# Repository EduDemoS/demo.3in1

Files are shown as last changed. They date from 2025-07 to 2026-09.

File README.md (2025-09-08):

# 3×1 Demonstrator: Solar, wind and water harvesting in a single educational project

The 'Edudemos' project launches an innovative 3×1 demonstrator that combines three powerful educational resources in a single device. This multifunctional demonstrator allows students to explore and experiment with solar energy harvesting, wind energy, and water harvesting, all in a single project.

The 3×1 demonstrator is designed for students in vocational training centers and schools to build with the help of their teachers, integrating fundamental concepts of renewable energy and resource management.

This repository contains all necessary files and is structured as follows:

- [doc](doc) contains documentation such as 
  - [details.md](doc/details.md)
  - assembly manual
  - bill of material
- [code](code) contains program code to run the model
- [model](model) contains the printable 3D model

# Licensing
Please note: different licenses apply depending on the type of content.

All documents and 3d models (files ending with .pdf and .stl) are licensed under [CC-BY-NC-SA 4.0](https://creativecommons.org/licenses/by-nc-sa/4.0/).

All files containing code are licensed under [GNU GPL V3](https://www.gnu.org/licenses/gpl-3.0.txt).

# Disclaimer
Funded by the European Union. Views and opinions expressed are however those of the author(s) only and do not necessarily reflect those of the European Union or the European Education and Culture Executive Agency (EACEA). Neither the European Union nor EACEA can be held responsible for them.

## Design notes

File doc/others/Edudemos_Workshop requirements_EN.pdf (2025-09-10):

# EDUcating through Sustainable DEMOnstrators

# Workshop requirements

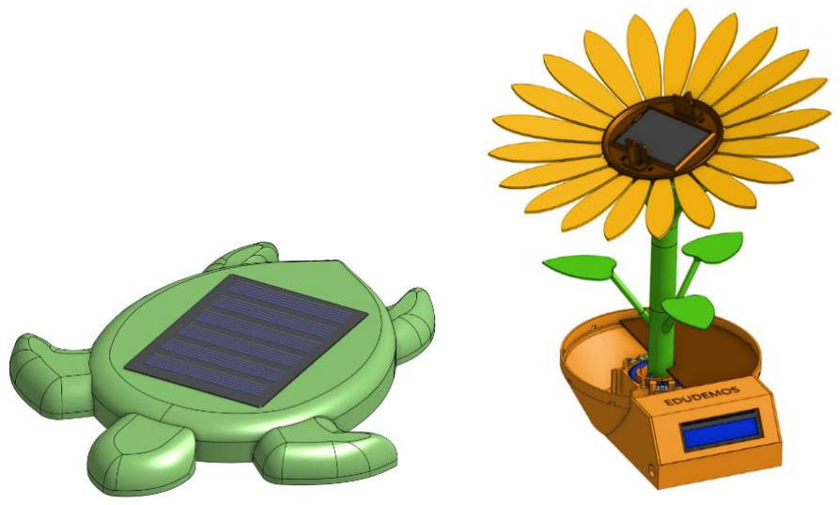
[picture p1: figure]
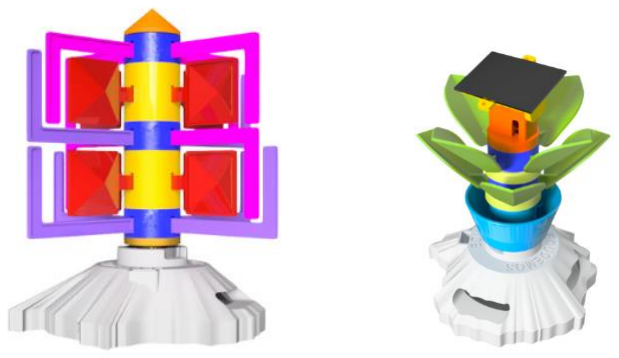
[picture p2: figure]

Funded by the European Union. Views and opinions expressed are however those of the author(s) only and do not necessarily reflect those of the European Union or the European Education and Culture Executive Agency (EACEA). Neither the European Union nor EACEA can be held responsible for them.

EduDemoS 3in1 © 2025 by Gerda Stetter Stiftung – Technik macht Spaß! is licensed under Creative Commons Attribution-NonCommercial-ShareAlike 4.0 International. To view a copy of this license, visit https://creativecommons.org/licenses/by-nc-sa/4.0/

# EduDemoS Workshop

During the EduDemoS Workshop we will develop three different Sustainable Demonstrators:

### 1. Turtle

2. 3x1 Modular Demonstrator

### 3. Sun-Tracker (Sunflower)

To know more about these demonstrators and the EduDemoS Project, visit the website https://edudemos.eu/en/

Every demonstrator has a guide explaining how to build it. To be prepared for the Workshop, you can download and read these guides beforehand.

- From the homepage of the website, click on Demonstrators in the top menu. Look for Turtle, Solar-Tracking and 3x1 Demonstrator, then select Guide for each of them and download the pdf file.
- For the 3x1 Demonstrator you can download the guide in English or Spanish. See the name of the file to identify them.
- There are also some videos that illustrate how to assemble the 3x1 demonstrator.

# Technical requirements

To be able to successfully complete the Edudemos Workshop, you will need the following:

- Bring your laptop
- Have Arduino IDE installed
- Have the boards ESP8266 and ESP32 installed in Arduino
- Have the necessary libraries installed in Arduino
- Have the CP210x Driver installed

Below there is a guide explaining how to download and install everything you need.

# Installation Guide

# What is the Arduino IDE?

The Arduino IDE (Integrated Development Enviroment) is the software used to write, compile and upload code to your board. (In this case the ESP32-WROOM-DA and the ESP8266.)

# Downloading and installing the Arduino IDE:

### Step 1: Go to the Arduino Website

Open your web browser and visit the official Arduino website: https://www.arduino.cc/

### Step 2: Navigate to the Arduino IDE Download Page

From the homepage, click on Products in the top menu. Look for Software, then select Arduino IDE. Or go directly to this link: https://www.arduino.cc/en/software/#ide

### Step 3: Choose Your Operating System

On the Downloads page, select the appropriate version of the Arduino IDE for your operating system (Windows, macOS, or Linux).

- Recommended donwload: Windows Win 10 and newer, 64 bits

### Step 4: Download the Installer

Click on the download link, and if prompted, you can choose to contribute or simply click just download without contributing.

### Step 5: Install the Arduino IDE

- For Windows:
- Run the downloaded .exe file.
- Follow the installation wizard to install the IDE.
- Check the option to install the USB driver when prompted.
- For macOS:
- Open the downloaded .dmg file.
- Drag the Arduino IDE to the Applications folder.
- For Linux:
- Extract the downloaded .tar.xz file.
- Run the install.sh script in the terminal.

### Step 6: Verify Installation

Open the Arduino IDE to ensure it launches correctly.

# Cofiguring the Arduino IDE for the Sunflower and Turtle Demonstrators:

### Step 1: Add the ESP8266 Board URL

To use the ESP8266 with the Arduino IDE, you need to include the appropriate URL in the IDE's preferences:

1. Open the Arduino IDE
2. Go to File > Preferences (on macOS, this might be under Arduino > Preferences)
3. In the Additional Board Manager URLs field, paste the following URL: http://arduino.esp8266.com/stable/package_esp8266com_index.json
4. If there are already other URLs listed, separate them with a comma
5. Activate Auto save and Automatic and then click OK. See the image below

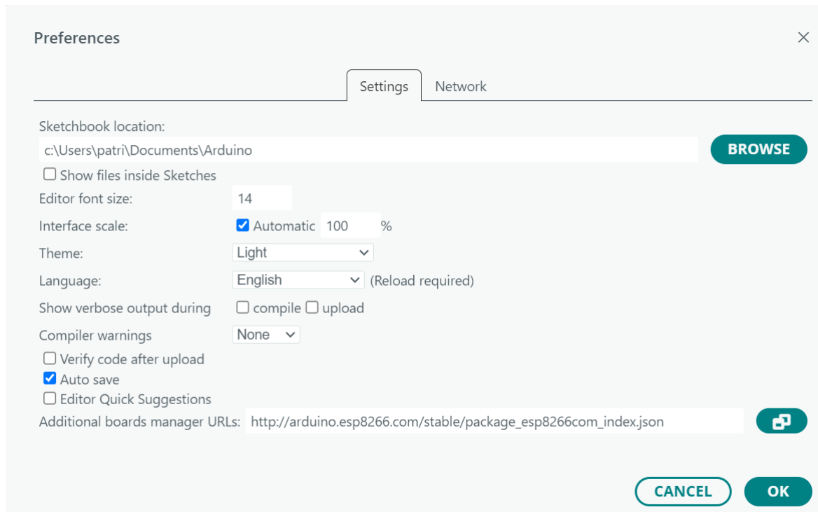
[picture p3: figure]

### Step 2: Install the ESP8266 Board Package

1. Go to Tools > Board > Boards Manager
2. In the search bar, type ESP8266
3. Select esp8266 by ESP8266 Community and click Install/update
4. Wait for the installation to complete

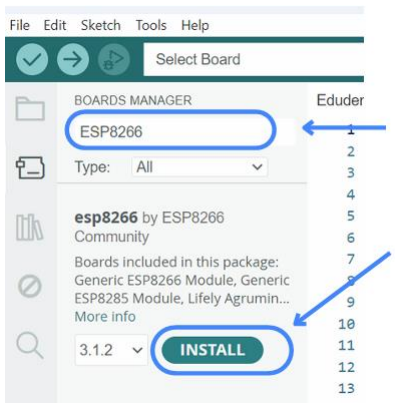
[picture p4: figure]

### Step 3: Select the ESP8266 Board

1. Go to Tools > Board and select Generic ESP8266 Module

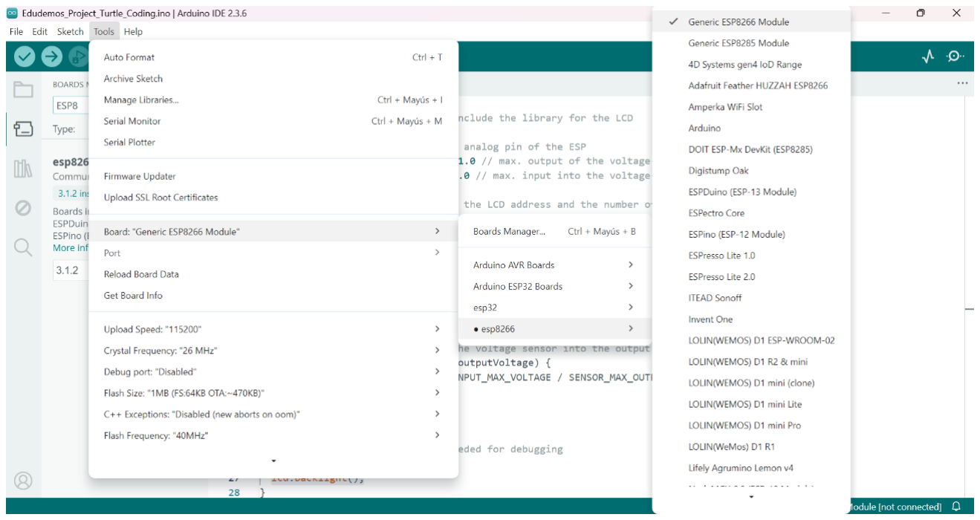
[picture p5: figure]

# Cofiguring the Arduino IDE for the 3x1 Demonstrator:

### Step 1: Add the ESP32 Board URL

To use the ESP32 with the Arduino IDE, you need to include the appropriate URL in the IDE's preferences:

1. Open the Arduino IDE
2. Go to File > Preferences (on macOS, this might be under Arduino > Preferences)
3. In the Additional Board Manager URLs field, paste the following URL: https://espressif.github.io/arduino-esp32/package_esp32_index.json
4. If there are already other URLs listed, separate them with a comma
5. Activate Auto save and Automatic and then click OK. See the image below

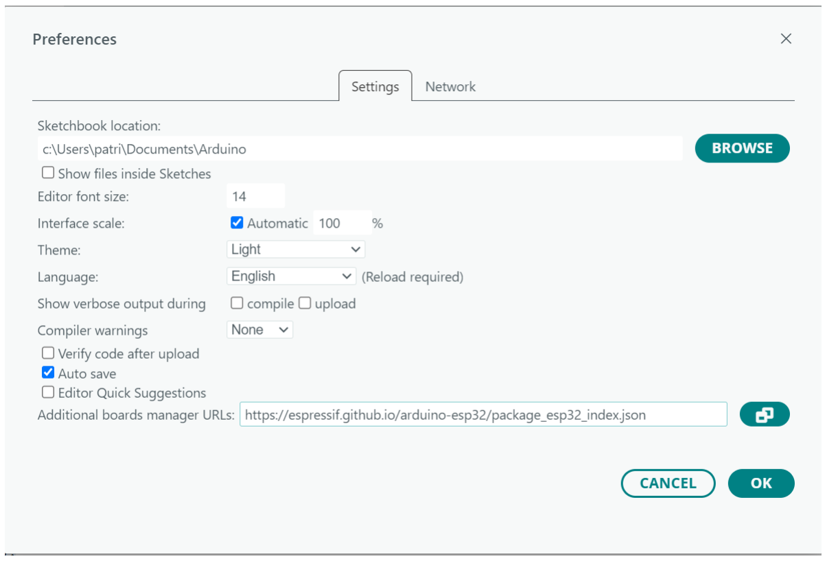
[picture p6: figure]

### Step 2: Install the ESP32 Board Package

1. Go to Tools > Board > Boards Manager
2. In the search bar, type ESP32
3. Select esp32 by Espressif Systems and click Install/update
4. Wait for the installation to complete

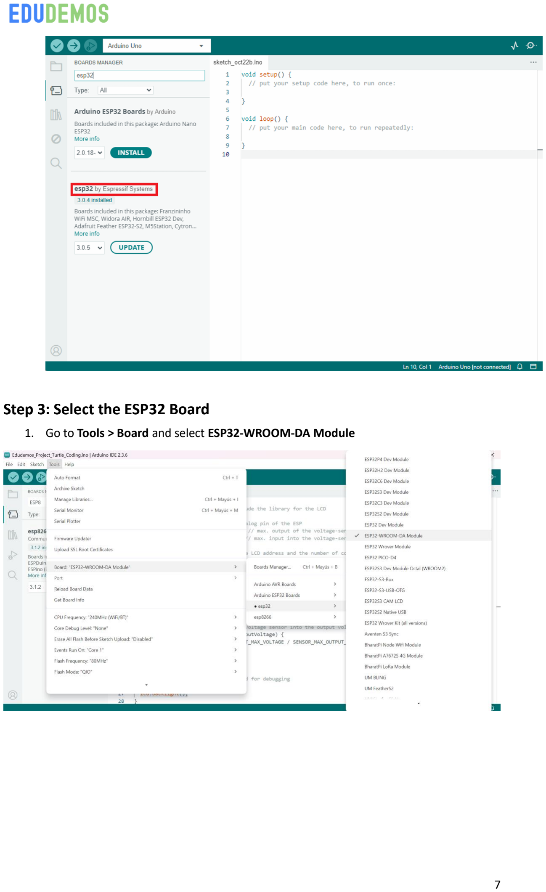
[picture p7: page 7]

### Step 3: Select the ESP32 Board

1. Go to Tools > Board and select ESP32-WROOM-DA Module

# Download the Missing Libraries to Run the Code of the Turtle and Sun-Tracker Demonstrators

### Step 1: Download the Libraries:

Go to the EduDemoS website https://edudemos.eu/en/demonstrators/ > Solar-Tracking and click on the Programming button. Dowload the folder called “libraries”.

### Step 2: Move the Libraries to the Correct Folder

- Navigate to the folder where your Arduino sketches are stored (e.g., Documents/Arduino/libraries on Windows or ~/Documents/Arduino/libraries on macOS/Linux).
- Create a new folder in the libraries directory with the same name as the library (e.g., LiquidCrystal_I2C). Do this with each folder.
- Move the extracted library folder into this newly created folder.

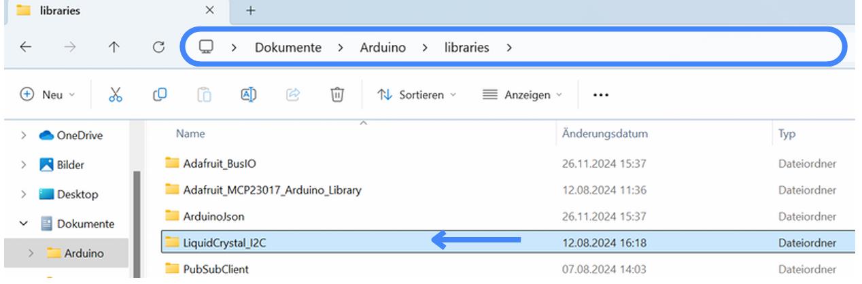
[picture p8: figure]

- Once the library is in the correct folder, it will be available for use in your Arduino IDE.

# Where to Find the Code

The code for the Turtle and the Solar-Tracking is available on the EduDemoS website under the Programming button of each demonstrator. https://edudemos.eu/en/demonstrators/

# Running the Code

- Open the Arduino IDE and load the turtle code into a new sketch. Finally you can click on the tick icon to verify the code.

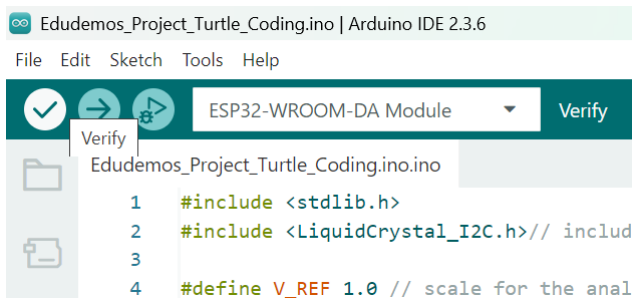
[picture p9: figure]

- A window will open showing the progress while compiling the sketch. If it compiles without any errors, everything is well installed. Otherwise, check again the libraries installation.
- Do this again with the Solar-Tracking code.

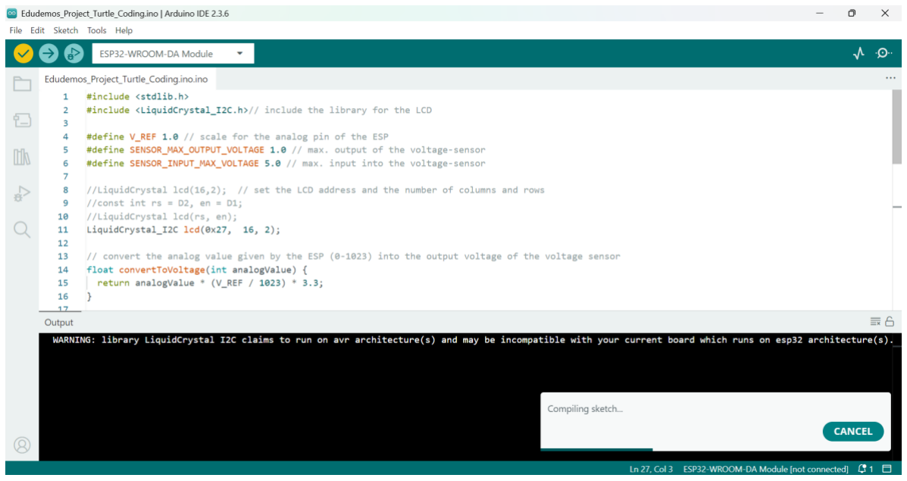
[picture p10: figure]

# Download the Missing Libraries to Run the Code of the 3x1 Demonstrator

### Step 1: Download the Libraries:

Go to the EduDemoS website GitHub - Gadeschii/EDUDEMOS (https://github.com/Gadeschii/EDUDEMOS) and click on src/main. Dowload the folder called “libraries.zip”.

### Step 2: Extract the ZIP File

Extract the downloaded ZIP file on your computer using a ZIP extractor such as WinRAR, 7-Zip, or the default extractor of your operating system.

### Step 3: Move the Libraries to the Correct Folder

- Navigate to the folder where your Arduino sketches are stored (e.g., Documents/Arduino/libraries on Windows or ~/Documents/Arduino/libraries on macOS/Linux).
- Create a new folder in the libraries directory with the same name as the library (e.g., ArduinoJson). Do this with each folder.
- Move the extracted library folder into this newly created folder.

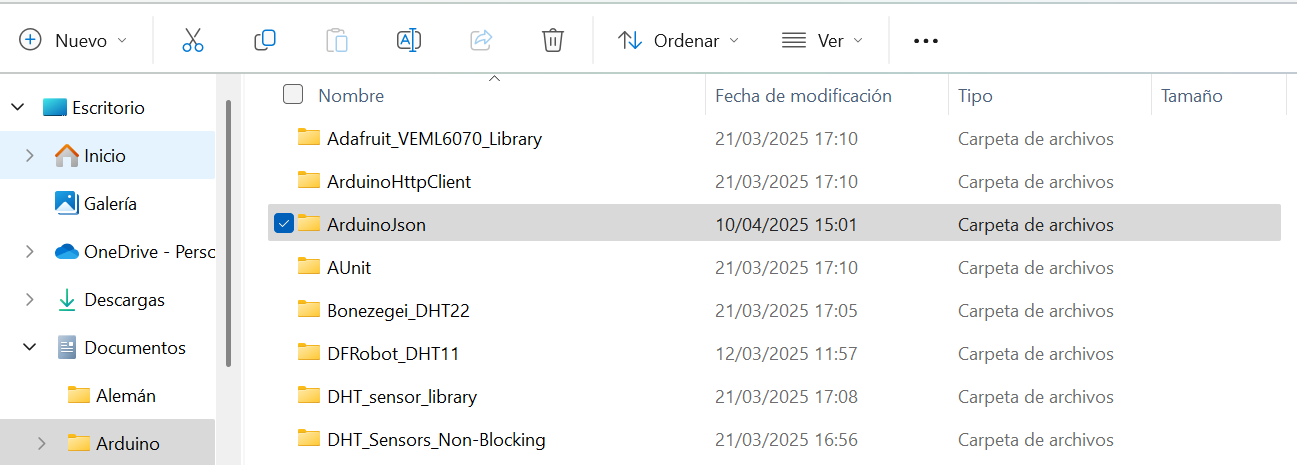
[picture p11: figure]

- Once the library is in the correct folder, it will be available for use in your Arduino IDE.

# Where to Find the Code

The code for the 3x1 Demonstrator is available on the EDUDEMOS GitHub repository: GitHub -Gadeschii/EDUDEMOS. (https://github.com/Gadeschii/EDUDEMOS) Click on src/main and dowload the file called “main_2”.

# Running the Code

- Open the Arduino IDE and load the 3x1 code into a new sketch. Finally you can click on the tick icon to verify the code.

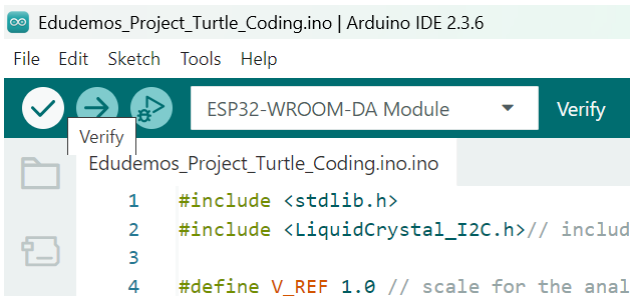
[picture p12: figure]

- A window will open showing the progress while compiling the sketch. If it compiles without any errors, everything is well installed. Otherwise, check again the libraries installation.

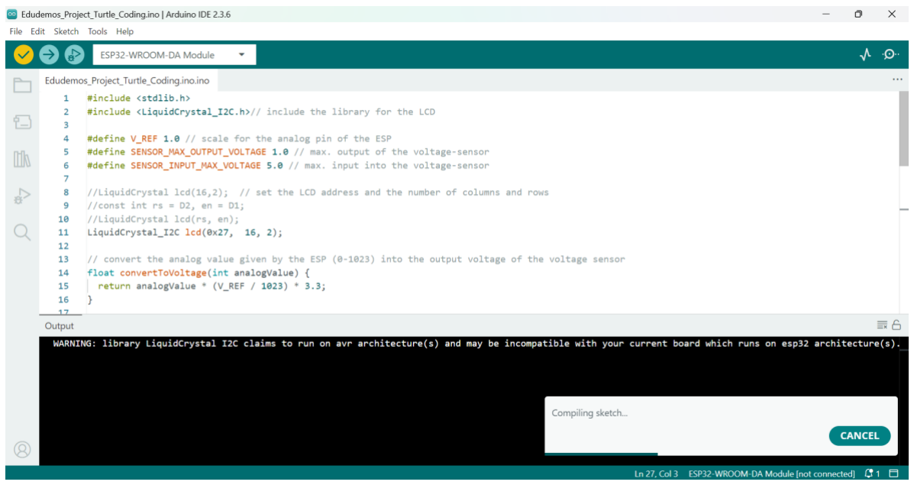
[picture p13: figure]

# Installing USB Driver

You may need to install the appropriate USB-to-Serial driver. The boards we are using have the CP210x chip:

- Download the Driver
- Go to the official Silicon Labs website: https://www.silabs.com/developer-tools/usb-to-uart-bridge-vcp-drivers?tab=downloads (https://www.silabs.com/developer-tools/usb-to-uart-bridge-vcp-drivers?tab=downloads)
- Download the appropriate version for your operating system. Recommended: CP210x Universal Windows Driver (Windows Universal Driver for Windows 10 and 11).
- Extract the downloaded ZIP folder on your computer using a ZIP extractor such as WinRAR, 7-Zip, or the default extractor of your operating system.
- Inside the folder click on the following file and click install/open and allow the program to make changes in your computer:

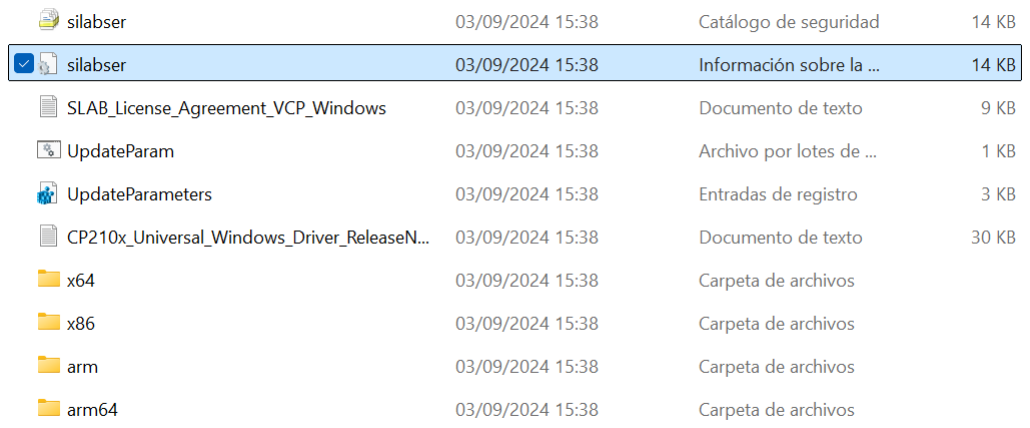
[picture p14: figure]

- Restart your computer after installing the driver.

# Congratulations!

You have successfully installed everything you need for the EduDemoS Workshop.

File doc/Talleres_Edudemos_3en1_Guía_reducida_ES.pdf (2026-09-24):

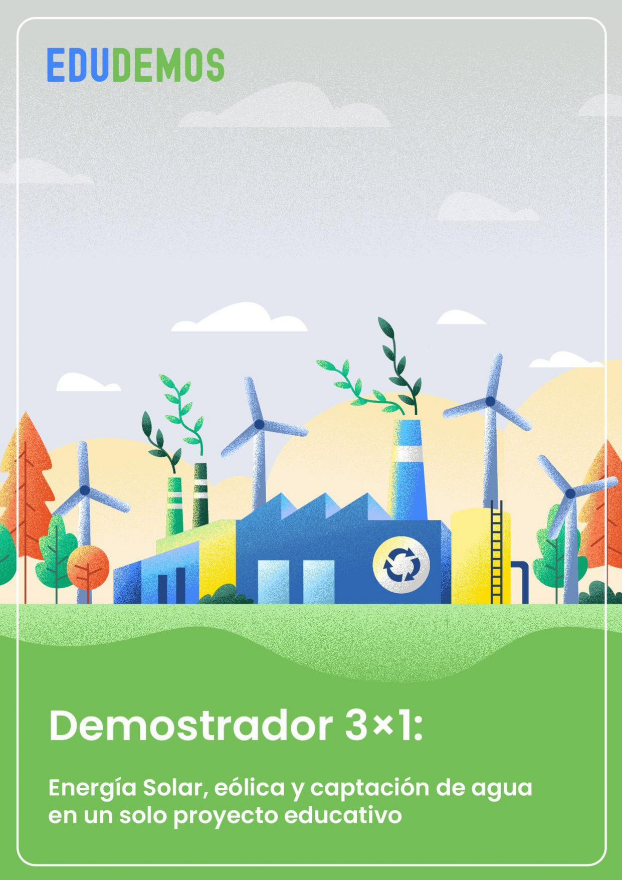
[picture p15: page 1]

# EDUDEMOS

# Financiado por la Unión Europea. Las opiniones y puntos de vista expresados solo comprometen a su(s) autor(es) y no reflejan necesariamente los de la Unión Europea o los de la Agencia Ejecutiva Europea de Educación y Cultura (EACEA). Ni la Unión Europea ni la EACEA

pueden ser considerados responsables de ellos.

EduDemoS 3in1 © 2025 by Gerda Stetter Stiftung – Technik macht Spaß!,

# Sergio Alonso Fundation, FINNOVA REGIO, GBS St. Gallen e IES El Rincón is licensed under

# Creative Commons Attribution-NonCommercial-ShareAlike 4.0 International. To view a copy of this license, visit https://creativecommons.org/licenses/by-nc-sa/4.0/

1

Financiado por la Unión Europea. Las opiniones y puntos de vista expresados solo comprometen a su(s) autor(es) y no reflejan necesariamente los de la Unión Europea o los de la Agencia Ejecutiva Europea de Educación y Cultura (EACEA). Ni la Unión Europea ni la EACEA pueden ser considerados responsables de ellos.

# 1. ENSAMBLAJE DEL DEMOSTRADOR 3x1

El montaje del Demostrador 3x1 se realizará de forma modular, abordando cada sección por separado en los apartados correspondientes de esta guía. Este enfoque busca simplificar el proceso y facilitar su comprensión, permitiendo que el montaje sea claro y accesible para quienes lo lleven a cabo. Cada paso está diseñado con el objetivo de garantizar un resultado funcional y efectivo, incluso para quienes no cuenten con

experiencia previa en ensamblaje de demostradores.

Uno de los objetivos principales de este proyecto es fomentar la autonomía de los centros educativos, permitiéndoles crear sus propios demostradores si cuentan con impresoras 3D en sus instalaciones. Por esta razón, hemos puesto a disposición los archivos de impresión necesarios para la fabricación de los componentes, los cuales

pueden descargarse a través del siguiente enlace: Archivos de impresión 3D. (https://drive.google.com/drive/folders/1F19XPgi768G87Ds_K66nvXBx-3E4KJT6) Con esta

# herramienta, buscamos empoderar a las instituciones educativas para que integren

estos demostradores en sus actividades de forma independiente y eficiente.

# 1. 1. Listado de materiales

- 1 x ESP32 DEVKIT V1 de 30 pines - 2 x Mini breadboard de 170 puntos - 1 x Módulo DHT11, de ancho máximo 14 mm y puede o no tener led incluido - 10/12* x Cables macho-macho 10 cm - 5 x Cables macho-macho 20 cm - 3 x Cables macho-hembra 10 cm - 10 x Cables macho-hembra 20 cm - 5 x Resistencias de 1k ohmio - 1 x Condensador de 100nF / 0.1uF - 3 x Leds de colores (Rojo, Verde y Azul preferiblemente) - 1 x Placa solar dimensiones máximas: 45 mm x 60 mm - 1 x Sensor nivel de agua, 6 cm x 2 cm - 1 x Motor DC de corriente continua de 5V, dimensiones máximas: 28 mm - diámetro y 45 mm largo - 1 x Servomotor SG-90

2

- 1 x Detector de tensión - 2 x Fotoresistencias independientes GL5528 - 1 x Rodamiento 6203 puede ser del tipo zz o 2rs: 40 mm diámetro exterior, 17 - mm diámetro interior y 12 mm de alto - 3 x Espiga de madera: 8 mm de diámetro y 40mm de largo - 1 x Engranaje motor: 2 mm diámetro interior, 10 dientes y 5 mm alto - 1 x Cable de datos USB a microUSB - 1 x Cinta adhesiva de aluminio, 5 cm de ancho - 1 x Cinta adhesiva de doble cara, 3 cm de ancho

# * Si el Motor DC no viene con los cables soldados, se necesitarán 12 cables macho-

macho de 10 cm.

# Herramientas que podrías necesitar:

- Soldador: si el motor DC o el panel solar no vienen con cables.
- Destornillador plano de 2 mm: para el sensor de voltaje.

# 1. 2. Montaje del Demostrador de Agua + Solar

# 1. 2. 1. Montaje electrónico (Parte de Agua)

# Comenzaremos realizando el montaje del captador de agua. Para realizar este montaje completo necesitarás el siguiente material:

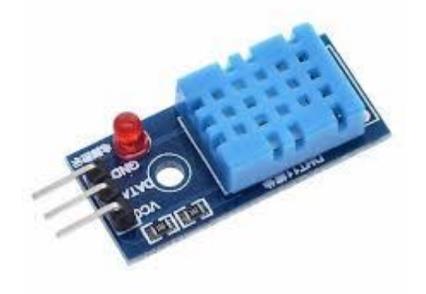
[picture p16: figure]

1 x Sensor DHT-11 | 3 x Resistencias de 1 kΩ

3

# Encargado de medir la temperatura y

la humedad ambientales.

# Usadas para limitar la corriente que

fluye por los diodos LED.

# 3 x LEDs de Colores (Rojo, Verde y Azul preferiblemente)

# 1 x Cable dupont (Macho-Macho) 10cm

# Empleados como indicadores visuales

del rango de la temperatura medida.

# Necesarios para realizar las conexiones entre los diferentes componentes en la

protoboard.

# 2 x Mini Breadboard

# 6 x Cable dupont (Macho-Hembra) 20cm

# Componente necesario para conectar la placa microcontroladora con los diferentes componentes

# Necesarios para realizar las conexiones entre los diferentes componentes en la

protoboard.

4

1 x Sensor nivel de agua | 1 x ESP32 DEVKIT V1 (30 pins)
Empleado para medir el nivel de agua en el tanque. | Encargado de ejecutar la programación que controla el funcionamiento de la electrónica.

El objetivo del montaje será obtener el valor de la temperatura y la humedad ambientales y, en función del valor de la temperatura, encender un LED u otro como indicadores de peligro por alta o baja temperatura. De esta manera si la temperatura está por debajo de los 20ºC se enciende el LED Azul, si se está por encima de los 25ºC se enciende el LED Rojo y si está entre ambos valores (entre 20 y 25ºC) se enciende el LED

Verde.

# El primer paso es colocar la placa con ESP32 sobre dos protoboard pequeñas para tener espacio suficiente para luego conectar los componentes que vamos a necesitar. A continuación se puede ver el resultado:

5

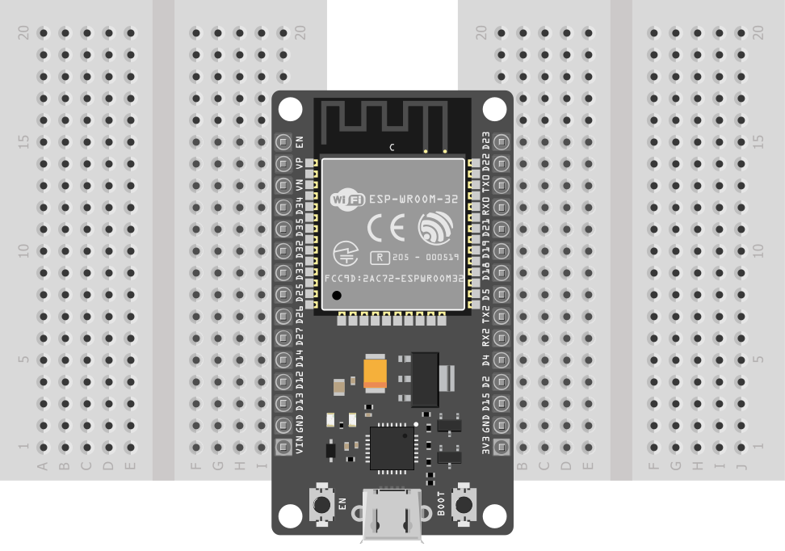
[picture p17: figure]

# Una vez tengamos el microcontrolador colocado en las dos protoboards, empezaremos a conectar los LEDs de colores con sus resistencias limitadoras. Vamos a empezar

colocando el LED Azul y una de las resistencias de 1 kΩ en serie. Conectaremos el positivo

# del LED en el pin D5, y utilizaremos cualquier pin GND para conectar el negativo del

circuito. A continuación se puede ver el montaje indicado.

Nota: El diodo LED nos indica la polaridad de la conexión a simple vista con el tamaño de sus patas de conexión. La más larga coincide con el ánodo, o positivo, y la más corta se trata del cátodo, o negativo. En el diagrama, la pata larga es la que va conectada en serie con la resistencia.

6

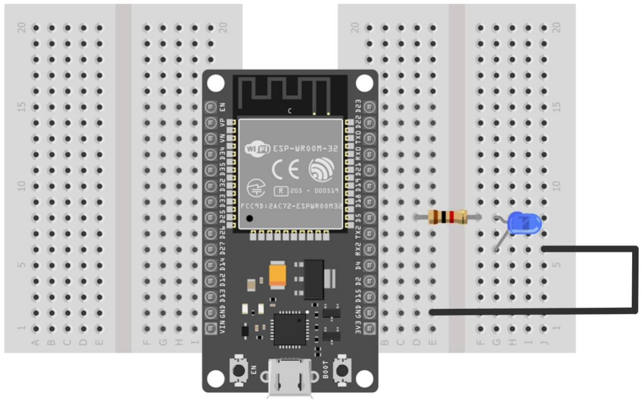
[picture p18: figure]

# Para comprobar el correcto funcionamiento del montaje, podemos cargar el siguiente código en el ESP32:

#define ledPin1Cold 5 // Definimos el pin donde está conectado el LED Azul

// Bloque de inicialización

void setup() {

// Configuramos el modo de funcionamiento del pin del LED como salida

pinMode(ledPin1Cold, OUTPUT);

}

// Bucle principal del código

void loop() {

digitalWrite(ledPin1Cold, LOW); // Apagamos el LED

delay(1000); // Esperamos 1 segundo = 1000 milisegundos

digitalWrite(ledPin1Cold, HIGH); // Encendemos el LED

delay(1000); // Esperamos 1 segundo

7

}

# Este pequeño programa hace parpadear el LED Azul, cambiando su estado entre encendido y apagado cada segundo. Si no funciona correctamente, comprueba que el

LED se encuentre bien orientado (recuerda que el terminal más largo es el positivo,

# mientras el corto es el negativo) y conectado adecuadamente con la resistencia

limitadora.

# El siguiente paso del montaje será añadir un segundo LED. Esta vez colocaremos y conectaremos el LED de color Verde en el pin D18 con su resistencia. Puedes ver el

esquema de montaje indicado en la siguiente imagen.

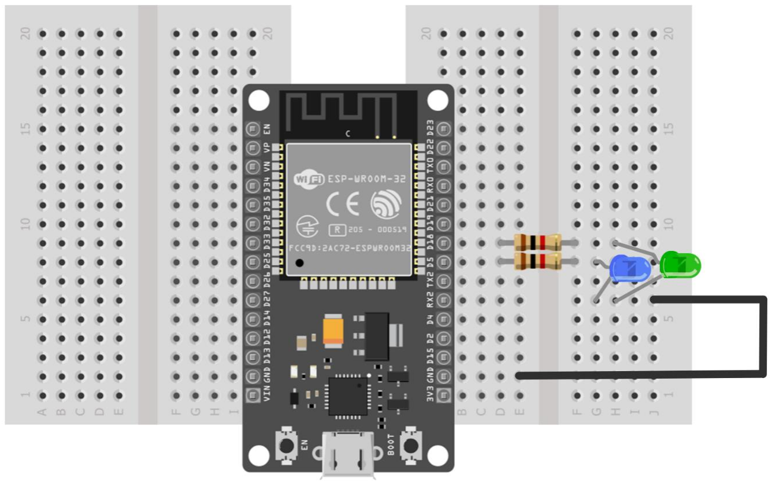
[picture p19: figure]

# Vamos a comprobar de nuevo que el montaje es correcto. Vamos a utilizar ahora el código que encontrarás a continuación para verificar que el nuevo LED también está

adecuadamente colocado.

8

#define ledPin1Cold 5 // Definimos el pin donde está conectado el LED Azul

#define ledPin2Good 18 // Definimos el pin donde está conectado el LED Verde

// Bloque de inicialización

void setup() {

// Configuramos el modo de funcionamiento de los pines de los LED como salida

pinMode(ledPin1Cold, OUTPUT);

pinMode(ledPin2Good, OUTPUT);

}

// Bucle principal del código

void loop() {

digitalWrite(ledPin1Cold, LOW); // Apagamos el LED Azul

digitalWrite(ledPin2Good, LOW); // Apagamos el LED Verde

delay(1000); // Esperamos 1 segundo = 1000 milisegundos

digitalWrite(ledPin1Cold, HIGH); // Encendemos el LED Azul

digitalWrite(ledPin2Good, HIGH); // Encendemos el LED Verde

delay(1000); // Esperamos 1 segundo

}

Como puedes ver, el objetivo del código es el mismo: encender y apagar, esta vez,

# ambos LED cambiando de estado cada segundo. Si el LED Azul y el Verde cambian de estado correctamente, podemos dar por válido el montaje actual y continuar con el

siguiente paso.

# Para terminar de montar los LEDs de colores que necesitamos para cumplir con el objetivo establecido con esta parte del Demostrador, necesitamos conectar el último LED de color Rojo en el pin D19. Procede a montar el diodo LED y la última resistencia

correspondiente, como se muestra en la siguiente imagen.

9

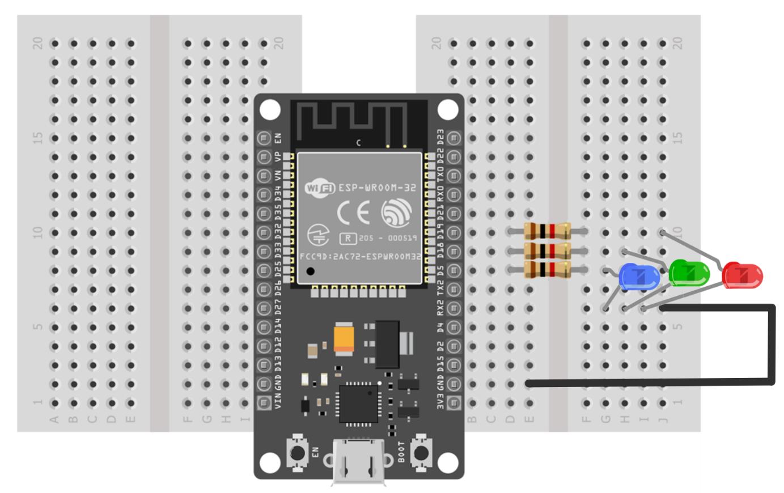
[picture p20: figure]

# Comprobaremos que está correcto realizando la misma programación que en los casos

anteriores, generando un parpadeo, ahora, en los tres LEDs de colores. El código para ello es el que sigue.

#define ledPin1Cold 5 // Definimos el pin donde está conectado el LED Azul

#define ledPin2Good 18 // Definimos el pin donde está conectado el LED Verde

#define ledPin3Heat 19 // Definimos el pin donde está conectado el LED Rojo

// Bloque de inicialización

void setup() {

// Configuramos el modo de funcionamiento de los pines de los LED como salida

pinMode(ledPin1Cold, OUTPUT);

pinMode(ledPin2Good, OUTPUT);

pinMode(ledPin3Heat, OUTPUT);

}

// Bucle principal del código

void loop() {

10

digitalWrite(ledPin1Cold, LOW); // Apagamos el LED Azul

digitalWrite(ledPin2Good, LOW); // Apagamos el LED Verde

digitalWrite(ledPin3Heat, LOW); // Apagamos el LED Rojo

delay(1000); // Esperamos 1 segundo = 1000 milisegundos

digitalWrite(ledPin1Cold, HIGH); // Encendemos el LED Azul

digitalWrite(ledPin2Good, HIGH); // Encendemos el LED Verde

digitalWrite(ledPin3Heat, HIGH); // Encendemos el LED Rojo

delay(1000); // Esperamos 1 segundo

}

# El próximo paso es agregar y conectar el sensor DHT11 en el pin D32, ya sea como un componente individual o en un módulo. A continuación se presenta el montaje realizado

hasta este momento junto con las conexiones del sensor DHT11.

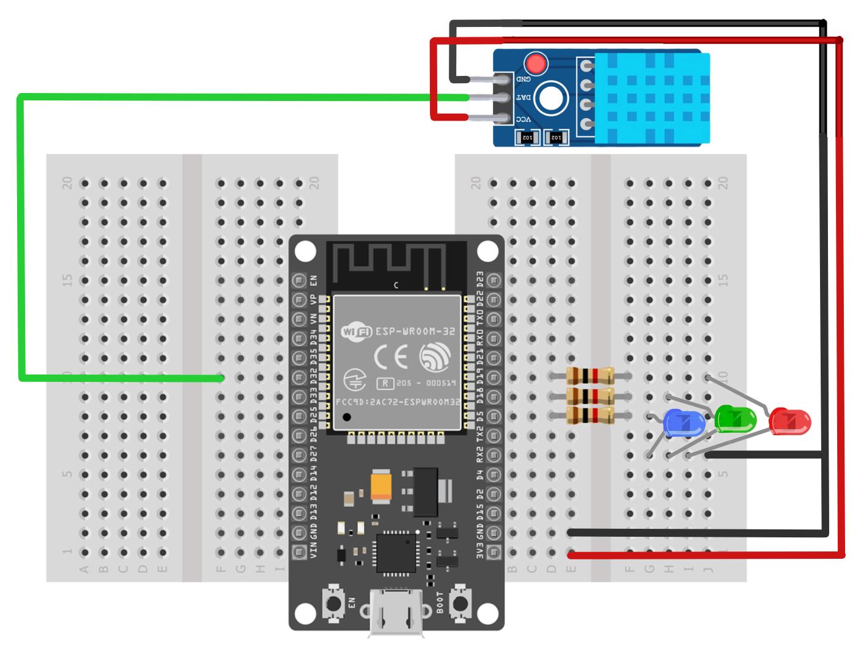
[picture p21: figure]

11
Nota: Comprobar que las conexiones GND y VCC del sensor DHT11 se corresponden con la descripción de los pines reales del componente, ya que puede ser diferente a la que aparece en el diagrama.

Pasamos a comprobar el correcto funcionamiento del sensor DHT-11. A continuación,

dispones de un código de prueba de todo el montaje realizado para esta parte del montaje. Carga el programa y verás cómo, además de que los LEDs de colores parpadean como han hecho hasta ahora, la placa con ESP32 enviará por el Monitor Serial (puedes ver el botón donde abrirlo en la siguiente imagen) cada par de segundos las medidas obtenidas de temperatura ambiental (en ºC) y humedad relativa del aire

(en %).

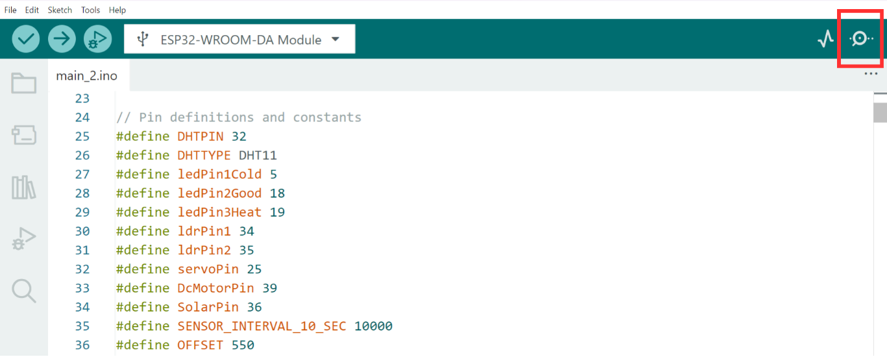
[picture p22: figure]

#include <DHT.h> // Incluimos la librería necesaria para controlar de DHT

#define ledPin1Cold 5 // Definimos el pin donde está conectado el LED Azul

#define ledPin2Good 18 // Definimos el pin donde está conectado el LED Verde

#define ledPin3Heat 19 // Definimos el pin donde está conectado el LED Rojo

#define DHTPIN 32 // Definimos el pin donde está conectado el DHT

#define DHTTYPE DHT11 // Definimos el tipo de sensor DHT que vamos a utilizar

// Creamos un objeto de tipo DHT con la configuración correspondiente

DHT myDHT11(DHTPIN, DHTTYPE);

// Bloque de inicialización

void setup() {

// Configuramos el modo de funcionamiento de los pines de los LED como salida

12

pinMode(ledPin1Cold, OUTPUT);

pinMode(ledPin2Good, OUTPUT);

pinMode(ledPin3Heat, OUTPUT);

// Inicializamos el monitor Serial

Serial.begin(115200);

// Inicializamos el sensor DHT

myDHT11.begin();

}

// Bucle principal del código

void loop() {

digitalWrite(ledPin1Cold, LOW); // Apagamos el LED Azul

digitalWrite(ledPin2Good, LOW); // Apagamos el LED Verde

digitalWrite(ledPin3Heat, LOW); // Apagamos el LED Rojo

delay(1000); // Esperamos 1 segundo = 1000 milisegundos

digitalWrite(ledPin1Cold, HIGH); // Encendemos el LED Azul

digitalWrite(ledPin2Good, HIGH); // Encendemos el LED Verde

digitalWrite(ledPin3Heat, HIGH); // Encendemos el LED Rojo

delay(1000); // Esperamos 1 segundo

//Obtenemos las medidas del sensor DHT

float temperatura = myDHT11.readTemperature();

float humedad = myDHT11.readHumidity();

// Mostramos los valores por monitor Serial

Serial.print("Temperatura: ");

Serial.println(temperatura);

Serial.print("Humedad: ");

Serial.println(humedad);

}

# Con el monitor abierto, comprueba que el desplegable que se ubica más a la derecha sobre el propio Monitor tenga seleccionado el valor “115200”. Ahora podrás ver los datos que envía el ESP32 tomados del DHT-11 de manera constante y verificar que el montaje

hasta este punto funciona correctamente.

13

# El siguiente componente que se va a añadir va a ser el módulo de sensor de nivel de agua. Conectamos el sensor en el pin VN. En la siguiente imagen se ve como quedaría el montaje:

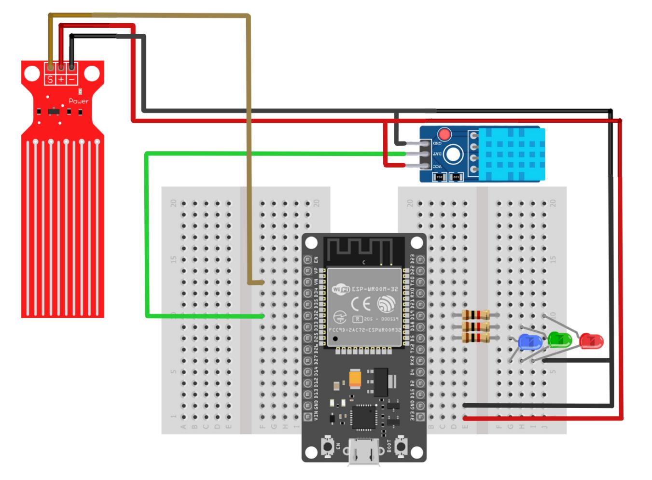
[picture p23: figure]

# Ahora vamos a verificar el funcionamiento del sensor de nivel de agua leyendo y mostrando por el monitor serial constantemente el valor medido del sensor:

//Water sensor calibration

const int WaterSensorPin = 39; // Analog Value from VN PIN

void setup() {

Serial.begin(115200);

}

void loop() {

int sensorValue; // Variable to store sensor values

sensorValue = analogRead(WaterSensorPin); // Read the value from the sensor

Serial.println(sensorValue); // Print value in serial monitor

delay(100);

14

}

15

# 1. 2. 2. Montaje electrónico (Parte Solar)

# Comenzaremos realizando el montaje del componente solar. Para realizar este montaje completo necesitarás el siguiente material:

# 1 x Servomotor SG-90

# 2 x Fotoresistencias independientes

# Utilizado para mover el Demostrador

solar y orientarlo hacia la luz solar.

# Empleados para medir el nivel de

luminosidad recibida.

# 2 x Resistencias 1k ohm

# 9 x Cable dupont (Macho-Macho) 10cm

# Utilizadas solamente junto con las LDR independientes para montar un partidor de tensión controlado por

intensidad lumínica.

# Necesarios para realizar las conexiones entre los diferentes componentes en la

protoboard.

16

# 5 x Cable dupont (Macho-Macho) 20cm

# 3 x Cable dupont (Macho-Hembra) 10cm

# Necesarios para realizar las conexiones entre los diferentes componentes en la

protoboard.

# Necesarios para realizar las conexiones entre los diferentes componentes en la

protoboard.

# 4 x Cable dupont (Macho-Hembra) 20cm

# 1 x Detector de tensión

# Necesarios para realizar las conexiones entre los diferentes componentes en la

protoboard.

# Necesarios para realizar las conexiones entre los diferentes componentes en la

protoboard.

# 1 x Panel solar

17
Empleado para detectar luz solar. El objetivo del montaje será obtener la orientación de la incidencia de la luz solar con las

# LDR y rotar el Demostrador para que incida la mayor cantidad de rayos solares sobre el

panel.

# El montaje del componente solar va a comenzar desde el último montaje que se vio en

el apartado anterior. En este montaje se añade una LDR y una resistencia en serie,

# formando un partidor de tensión controlado por la intensidad lumínica. Para obtener el

valor del sensor se va a utilizar la salida digital del mismo, que se va a conectar al pin

# D34 del ESP32. El montaje se puede ver a continuación:

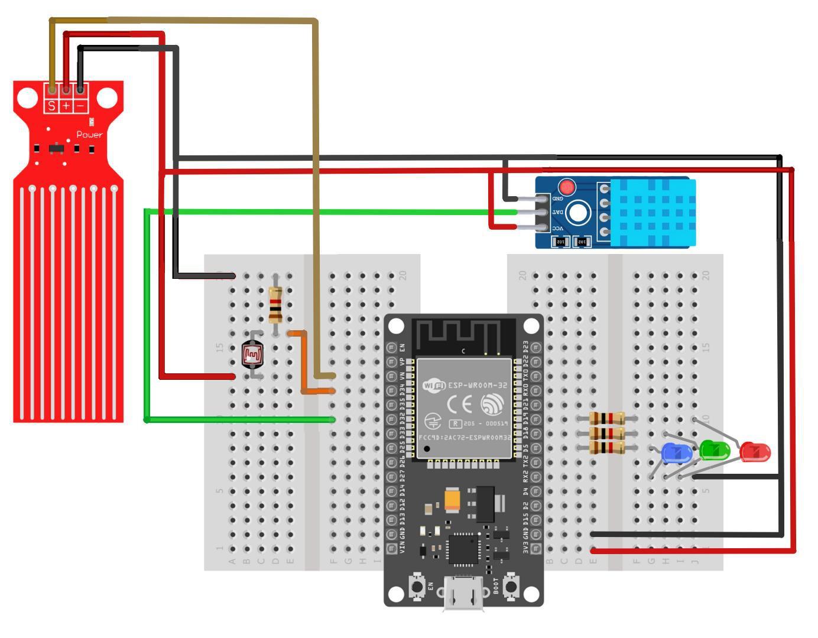
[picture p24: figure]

18
Para comprobar el funcionamiento de los nuevos elementos añadidos al montaje,

# vamos a emplear un código que solamente tome la medida de la LDR para encender el LED Rojo con mayor o menor intensidad según la luminosidad medida por la

fotorresistencia. Puedes ver el código a cargar a continuación.

#define ldrPin1 34 // Definimos el pin donde está conectado la LDR

// Bloque de inicialización

void setup() {

// Inicializamos el monitor serial

Serial.begin(115200);

}

// Bucle principal del código

void loop() {

// Tomamos la lectura del pin donde se encuentra la LDR

int lectura_ldr_1 = analogRead(ldrPin1);

// Mostramos el valor por el monitor Serial

Serial.print("Luminosidad 1: ");

Serial.println(lectura_ldr_1);

}

# A continuación se debe añadir la segunda LDR con su resistencia. Para obtener el valor

de la lectura de este sensor se va a utilizar la salida digital, como en el caso anterior,

# pero esta se va a conectar al pin D35. A continuación se puede ver el montaje con

ambas LDR para la parte actual del Demostrador.

19

Comprobemos que se ha conectado correctamente empleando el siguiente código,

# que es muy similar al anterior pero mostrando el valor de la medida de ambas

fotorresistencias.

#define ldrPin1 34 // Definimos el pin donde está conectado la primera LDR

#define ldrPin2 35 // Definimos el pin donde está conectado la segunda LDR

// Bloque de inicialización

void setup() {

// Inicializamos el monitor serial

Serial.begin(115200);

}

20

// Bucle principal del código

void loop() {

// Tomamos las lecturas de los pines donde se encuentran las LDR

int lectura_ldr_1 = analogRead(ldrPin1);

int lectura_ldr_2 = analogRead(ldrPin2);

// Mostramos el primer valor por el monitor Serial

Serial.print("Luminosidad 1: ");

Serial.println(lectura_ldr_1);

// Mostramos el segundo valor por el monitor Serial

Serial.print("Luminosidad 2: ");

Serial.println(lectura_ldr_2);

}

# El siguiente componente que se va a añadir en el montaje es un servomotor. Este se va a conectar a ambas lineas de alimentación (cable rojo a la positiva y cable negro a la

negativa) y el cable amarillo (que es la señal de control) se va a conectar al pin D25.


21

# Comprobaremos el funcionamiento del servomotor cargando el siguiente código en la placa ESP32 que realiza un barrido moviendo el servo entre las posiciones de 0º, 90º y

180º, en bucle, una y otra vez.

#include <ESP32Servo.h> // Incluir la librería necesaria para controlar el servomotor

#define servoPin 25 // Definimos el pin donde está conectado el servomotor

// Creamos un objeto de tipo Servo para controlarlo

Servo myServo;

// Bloque de inicialización

void setup() {

// Asociamos el servo que creamos al pin donde está conectado

myServo.attach(servoPin);

// Colocamos el servo en una posición inicial de 0º

myServo.write(0);

}

// Bucle principal del código

void loop() {

myServo.write(0); // Movemos el servomotor a 0º

delay(1000); // Esperamos 1 segundo = 1000 milisegundos

myServo.write(90); // Movemos el servomotor a 90º

delay(1000); // Esperamos 1 segundo

myServo.write(180); // Movemos el servomotor a 180º

delay(1000); // Esperamos 1 segundo

}

Nota: Colocar la pestaña en el servo. No es necesario usar tornillos para sujetarla.

# El último componente que vamos a conectar al ESP32 será un detector de tensión. Este módulo se debe alimentar a ambas líneas de alimentación (Vcc y GND). La línea de

señal se va a conectar al pin VP.

22


# El último paso que falta para terminar el montaje electrónico es conectar el panel solar

al detector de tensión. A continuación, se ve cómo quedaría el montaje completo.

23

# Vamos a comprobar el funcionamiento del detector solar completo haciendo uso del siguiente código que simplemente lee la señal del módulo detector de tensión y

enciende el LED Azul si detecta voltaje.

#define ledPin1Cold 5 // Definimos el pin donde está conectado el LED Azul

#define detectorPin 36 // Definimos el pin donde está conectado el Detector de Tensión

// Bloque de inicialización

void setup() {

// Configuramos el modo de funcionamiento del pin del LED como salida

pinMode(ledPin1Cold, OUTPUT);

}

// Bucle principal del código

void loop() {

// Tomamos la lectura del Módulo Detector

bool tension_detectada = digitalRead(detectorPin);

// Comprobamos si hay tensión o no

if(tension_detectada) { // Sí hay tensión

digitalWrite(ledPin1Cold, HIGH); // Encendemos el LED Azul

} else { // No hay tensión

digitalWrite(ledPin1Cold, LOW); // Apagamos el LED Azul

}

}

# A continuación, dejamos un código test para comprobar que todos los sensores

obtienen | lecturas | y | funcionan | correctamente:

//include the necessary libraries

#include <ESP32Servo.h> // Libreria para controlar servomotores en el ESP32 #include "DHT.h" // Libreria para leer el sensor de temperatura/humedad DHT

// ---------- Pines ----------
const int LDR_PIN_EAST = 34; // Pin analogico donde esta conectado el LDR del lado Este

24

const int LDR_PIN_WEST = 35; // Pin analogico donde esta conectado el LDR del lado Oeste const int DHT_PIN = 32; // Pin digital donde esta conectado el sensor DHT11
const int LED_COLD_PIN = 5; // Pin digital del LED azul (indica frio)
const int LED_GOOD_PIN = 18; // Pin digital del LED verde (indica temperatura normal)
const int LED_HEAT_PIN = 19; // Pin digital del LED rojo (indica calor)
const int SOLAR_PIN | = 36; // Pin analogico donde esta conectado el panel solar
const int WATER_PIN | = 39; // Pin analogico donde esta conectado el sensor de nivel de agua
const int SERVO_PIN | = 25; // Pin PWM donde esta conectado el servomotor

// ---------- Constantes de comportamiento ----------
const int SERVO_TOLERANCE = 20; // Diferencia minima entre LDRs para mover el servo
const float SOLAR_THRESHOLD_UV = 10.0; // Umbral minimo en microvoltios para considerar luz solar valida const unsigned long LOOP_DELAY = 5000; // Tiempo de espera (ms) entre cada ciclo del loop

#define DHTTYPE DHT11 // Define el modelo de sensor DHT que se esta usando (DHT11)

// ---------- Objetos globales ----------
DHT dht(DHT_PIN, DHTTYPE); // Crea el objeto "dht" asociado al pin y tipo de sensor definidos
Servo myservo; | // Crea el objeto "myservo" para controlar el servomotor

// ---------- Estado ----------
int valldr1 = 0; | // Guarda la ultima lectura del LDR Este
int valldr2 = 0; | // Guarda la ultima lectura del LDR Oeste
int averageLdrValue = 0; // Guarda el promedio entre ambos LDR
int servopos = 90; // Posicion actual del servo, arranca centrado en 90 grados
float lastMicrovolts = 0; // Guarda el ultimo valor de microvoltios distinto que se imprimio (para detectar cambios)
int sensorValue; | // Guarda la lectura cruda del sensor de agua

void setup() {
Serial.begin(115200); // Inicia la comunicacion serial a 115200 baudios para ver datos en consola

analogReadResolution(12); // Configura las lecturas analogicas con resolucion de 12 bits (0-4095) analogSetAttenuation(ADC_11db); // Configura la atenuacion del ADC para leer voltajes hasta ~3.3V

pinMode(4, INPUT); | // Configura el pin 4 como entrada (reservado, no usado en este codigo)
pinMode(LED_COLD_PIN, OUTPUT); // Configura el pin del LED azul como salida pinMode(LED_GOOD_PIN, OUTPUT); // Configura el pin del LED verde como salida pinMode(LED_HEAT_PIN, OUTPUT); // Configura el pin del LED rojo como salida pinMode(LDR_PIN_EAST, INPUT); // Configura el pin del LDR Este como entrada pinMode(LDR_PIN_WEST, INPUT); // Configura el pin del LDR Oeste como entrada
dht.begin(); | // Inicializa el sensor DHT para empezar a leer
myservo.attach(SERVO_PIN); // Asocia el objeto servo al pin fisico definido myservo.write(servopos); // Mueve el servo a su posicion inicial (90 grados)

delay(1000); // Espera 1 segundo para que todos los sensores se estabilicen }

void loop() {
readSolarPanel(); // Lee el panel solar e imprime su resultado readTemperatureHumidity(); // Lee temperatura/humedad, actualiza LEDs e imprime el resultado readWaterLevel(); // Lee el sensor de agua e imprime el resultado readLdrAndMoveServo(); // Lee los LDR, mueve el servo e imprime el resultado

delay(LOOP_DELAY); // Espera antes de iniciar el siguiente ciclo de lectura }

25

// ============================================================ // Lectura del panel solar
// ============================================================
void readSolarPanel() {
Serial.println("----------------------------- Measured Solar (V) ---------------------------- "); // Encabezado de esta seccion en consola

int solarVoltagedV = analogRead(SOLAR_PIN); // Lee el valor crudo del ADC (0-4095) en el pin del panel solar
int solarVoltage = solarVoltagedV * 10; // Escala el valor crudo multiplicando por 10 (factor de calibracion)

Serial.print("Voltage of Solar Panel: "); // Imprime etiqueta del voltaje escalado
Serial.println(solarVoltage); | // Imprime el valor del voltaje escalado

float voltage = (solarVoltage / 4095.0) * 3.3; // Convierte el valor escalado a voltios reales (0-3.3V)

Serial.print("Measured voltage (V): "); // Imprime etiqueta del voltaje medido
Serial.println(voltage); | // Imprime el voltaje medido en voltios

float microvoltsSolar = voltage * 1000000.0; // Convierte el voltaje de voltios a microvoltios

Serial.print("Input voltage (uV): "); // Imprime etiqueta del voltaje en microvoltios Serial.println(microvoltsSolar); // Imprime el voltaje en microvoltios

if (microvoltsSolar < SOLAR_THRESHOLD_UV) { // Si la lectura esta por debajo del umbral definido...
microvoltsSolar = 0; | // ...se considera ruido y se fuerza a cero
}

if (microvoltsSolar != lastMicrovolts) { // Si el valor cambio respecto a la ultima lectura registrada...
Serial.print("Send voltage: "); | // ...imprime etiqueta indicando el nuevo valor
Serial.print(microvoltsSolar, 2); | // ...imprime el nuevo valor con 2 decimales
Serial.println(" uV"); | // ...imprime la unidad (microvoltios)

lastMicrovolts = microvoltsSolar; // Actualiza el ultimo valor registrado para la proxima comparacion }
}

// ============================================================ // Lectura de temperatura y humedad + control de LEDs
// ============================================================
void readTemperatureHumidity() {
Serial.println("----------------------- Measured Temperature / Humidity ----------------------- ");

float h = dht.readHumidity(); // Lee la humedad relativa del sensor DHT (%)
float t = dht.readTemperature(); // Lee la temperatura del sensor DHT (grados Celsius)

if (isnan(h) || isnan(t)) { // Si alguna de las dos lecturas falla (valor invalido)... Serial.println("Failed to read from DHT sensor!"); // ...imprime mensaje de error
return; | // ...y sale de la funcion sin continuar
}

Serial.print("Temperature: "); // Imprime etiqueta de temperatura
Serial.print(t); | // Imprime el valor de temperatura
Serial.print(" C, Humidity: "); // Imprime unidad de temperatura y etiqueta de humedad

26

Serial.print(h); | // Imprime el valor de humedad
Serial.print(" %"); | // Imprime unidad de humedad
Serial.println(); | // Salto de linea final

updateTemperatureLeds(t); // Actualiza el estado de los LEDs segun la temperatura leida }

// Enciende el LED correspondiente segun el rango de temperatura
void updateTemperatureLeds(float t) {
if (t > 30) { | // Si la temperatura es mayor a 30 grados (calor)...
digitalWrite(LED_HEAT_PIN, HIGH); // ...enciende el LED rojo
digitalWrite(LED_GOOD_PIN, LOW); // ...apaga el LED verde
digitalWrite(LED_COLD_PIN, LOW); // ...apaga el LED azul
Serial.println("Heat (rojo) is HIGH"); // Informa por consola que el LED de calor esta encendido
} else if (t < 20) { | // Si la temperatura es menor a 20 grados (frio)...
digitalWrite(LED_HEAT_PIN, LOW); // ...apaga el LED rojo
digitalWrite(LED_GOOD_PIN, LOW); // ...apaga el LED verde
digitalWrite(LED_COLD_PIN, HIGH); // ...enciende el LED azul
Serial.println("Cold (azul) is HIGH"); // Informa por consola que el LED de frio esta encendido
} else { | // Si la temperatura esta entre 20 y 30 grados (rango normal)...
digitalWrite(LED_HEAT_PIN, LOW); // ...apaga el LED rojo
digitalWrite(LED_GOOD_PIN, HIGH); // ...enciende el LED verde
digitalWrite(LED_COLD_PIN, LOW); // ...apaga el LED azul
Serial.println("Good (verde) is HIGH"); // Informa por consola que el LED de rango normal esta encendido }
}

// ============================================================ // Lectura del sensor de nivel de agua
// ============================================================
void readWaterLevel() {
Serial.println("----------------------------- Measured Water Level ----------------------------- ");

sensorValue = analogRead(WATER_PIN); // Lee el valor crudo del ADC en el pin del sensor de agua

if (sensorValue >= 2000) { // Si la lectura llega o supera el limite esperado (2000)... sensorValue = 1980; // ...la recorta a 1980 para evitar valores fuera de rango
}

float waterlevel = (sensorValue * 100) / 2000; // Convierte la lectura cruda a porcentaje (0-100%)

Serial.print("Water level: "); // Imprime etiqueta de nivel de agua
Serial.print(waterlevel); | // Imprime el valor de nivel de agua
Serial.println(" %"); | // Imprime unidad (porcentaje)
}

// ============================================================
// Lectura de LDRs y movimiento del servo
// ============================================================
// Este codigo esta preparado para leer los datos de los LDR de modo que a mayor cantidad de luz,
// mayor sera la respuesta analogica en consola. Por lo que el hardware, en el divisor de tension, en el palo del LDR debe estar conectado a VCC y el palo de la resistencia a GND.

void readLdrAndMoveServo() {
Serial.println("----------------------------- Measured LDR and Servo ----------------------------- ");

valldr1 = analogRead(LDR_PIN_EAST); // Lee el valor analogico del LDR ubicado al Este
valldr2 = analogRead(LDR_PIN_WEST); // Lee el valor analogico del LDR ubicado al Oeste

27

averageLdrValue = (valldr1 + valldr2) / 2; // Calcula el promedio entre ambas lecturas de luz

Serial.print("LDR 1: "); // Imprime etiqueta del LDR Este
Serial.print(valldr1); // Imprime el valor del LDR Este
Serial.print(" | LDR 2: "); // Imprime separador y etiqueta del LDR Oeste
Serial.println(valldr2); // Imprime el valor del LDR Oeste

Serial.print("Average LDR: "); // Imprime etiqueta del promedio
Serial.println(averageLdrValue); // Imprime el valor promedio de ambos LDR

if ((abs(valldr1 - valldr2) <= SERVO_TOLERANCE) || (abs(valldr2 - valldr1) <= SERVO_TOLERANCE)) { // Si la diferencia de luz esta dentro de la tolerancia...
// No se mueve el servo, se mantiene en su posicion actual
} else { // Si la diferencia de luz supera la tolerancia...
if (valldr1 > valldr2) { // ...y hay mas luz en el Este que en el Oeste... servopos = servopos + 10; // ...aumenta el angulo del servo 10 grados
}

if (valldr1 < valldr2) { // ...y hay mas luz en el Oeste que en el Este... servopos = servopos - 10; // ...disminuye el angulo del servo 10 grados }
}

if (servopos > 180) { // Si el angulo calculado supera el maximo permitido... servopos = 180; // ...lo limita a 180 grados
}

if (servopos < 0) { // Si el angulo calculado es menor al minimo permitido... servopos = 0; // ...lo limita a 0 grados
}

myservo.write(servopos); // Aplica el angulo final calculado al servomotor

Serial.print("Servo angle: "); // Imprime etiqueta del angulo del servo Serial.println(servopos); // Imprime el angulo final aplicado al servo }

28

# 1. 2. 3. Montaje Mecánico del Demostrador de Agua + Solar

# Los elementos que componen este demostrador son los siguientes:

Elemento | Cantidad | Descripción | Imagen
Base | 1

## Es la parte superior que asegura los componentes móviles, como

las palas y el eje del motor.

## Proporciona estabilidad y permite que el sistema funcione suavemente, facilitando la correcta transferencia de energía desde las palas al

generador.

Cajón | 1

## Es la base que conecta las diferentes secciones del dispositivo, proporcionando soporte estructural y asegurando una correcta alineación entre el motor, las palas y otros componentes esenciales para su

funcionamiento.

## Contenedor de agua

1

## Esta parte es capaz de almacenar el agua que cae en

él.

Hoja | 8

## Hoja que permite que los líquidos entren en el contenedor de agua

29

## Disco

Pequeño | 3

## Es un componente estático que no se mueve. Su función principal es actuar como parte del soporte

estructural del dispositivo,

## ayudando a mantener la correcta alineación y estabilidad

de los elementos.

## Disco

Estático | 2

## Disco que se mantiene fija para tapar y mantener la estabilidad

de la estructura.

Placa Sol | 1

## Parte que permite el movimiento del panel solar para su correcta orientación

Disco Solar | 1

## Disco que permite conectar el girador solar con un servomotor instalado y juntarlo con el resto

de la estructura.

# A continuación se muestra cómo se realiza el montaje del demostrador:

Nota: La cinta de aluminio se utiliza en la superficie de las hojas para optimizar la recolección de agua. La cinta de doble cara se utiliza en la parte trasera del panel solar para pegarlo en la pieza del “placa sol”.

El sensor de nivel de agua va colocado en unas ranuras dentro de la pieza “contenedor de agua”.

Al colocar los componentes electrónicos en el montaje mecánico, es necesario usar cables adicionales para alargar las conexiones de las LDR y de la placa solar.

30


31


32


33

34


35

# 1. 3. Montaje del Demostrador de viento

# 1. 3. 1. Montaje electrónico

# Comenzaremos realizando el montaje del Demostrador de viento. Para realizar este montaje completo necesitarás el siguiente material:


# 1 x Motor de Corriente Continua de 5V

# 1 x Condensador de 100nF / 1uF

# Empleado para generar voltaje con la

fuerza del viento.

# Utilizados para eliminar ruidos indeseados generados por el Motor de

CC.

# 2 x Resistencias de 1 kΩ

# 6 x Cable dupont (Macho-Macho) 10cm

# Utilizados en el divisor de tensión que permite tomar la lectura de tensión

generada por el Motor de CC.

# Necesarios para realizar las conexiones entre los diferentes componentes en la

protoboard.

36

2 x Mini Breadboard | Soldador de estaño
Componente necesario para conectar la placa microcontroladora con los diferentes componentes | sólo si el motor no tiene cables incluidos

# 1 x ESP32 DEVKIT V1 (30 pins)

# Encargado de ejecutar la programación que controla el funcionamiento de la

electrónica.

El objetivo del montaje será obtener la medida de la cantidad de voltaje generado por el motor, que irá unido a la estructura mecánica que girará por efecto de la fuerza del viento. Para poder realizar la medición con el ESP32 de la tensión obtenida por el movimiento de las aspas del Demostrador, debemos montar un partidor de tensión que

37

# reduzca el nivel máximo de tensión a obtener (5V) a uno que sea apto para el ESP32 (que trabaja a 3’3V). Con esto podremos obtener cuánto voltaje se está generando por

efecto del viento.
Para este nuevo montaje, será necesario crear un circuito desde el principio.

# Comenzaremos colocando el ESP32 en dos mini protoboards. A continuación, se muestra

el montaje correspondiente.


# A continuación, se procederá a montar un divisor de tensión. El punto intermedio de este divisor se conectará al pin D39 (VN). Además, es necesario conectar un condensador entre el terminal de este pin y GND, que servirá de filtro para las

variaciones indeseadas en la medida, tal y como se muestra en la imagen siguiente.

38


# El último paso en el montaje electrónico de este demostrador es conectar el motor al conjunto anterior, de manera que uno de sus terminales se une a GND y el otro terminal a la entrada del divisor de tensión montado antes. A continuación, se presenta este

montaje terminado.


39

# Vamos a comprobar que el montaje de este Demostrador funciona correctamente haciendo uso del siguiente fragmento de código en el que solamente leemos la salida del divisor de tensión que está unida al ESP32. Girando el rotor del motor, veremos como

la medición va dando diferentes valores a través del Monitor Serial.

// Bloque de inicialización

void setup() {

// Inicializamos el Monitor Serial

Serial.begin(115200);

}

// Bucle principal del código

void loop() {

// Tomamos la medida del pin que va a la salida del partidor de tensión

int medicion = analogRead(39);

// Mostramos la medida por el monitor serial

Serial.println(medicion);

}

40

# 1. 3. 2. Montaje Mecánico

# Los elementos que componen este demostrador son los siguientes:

Elemento | Cantidad | Descripción | Imagen
Base | 1

## Es la parte superior que asegura los componentes móviles, como

las palas y el eje del motor.

## Proporciona estabilidad y permite que el sistema funcione suavemente, facilitando la correcta transferencia de energía desde las palas al

generador.

Cajón | 1

## Es la base que conecta las diferentes secciones del dispositivo, proporcionando soporte estructural y asegurando una correcta alineación entre el motor, las palas y otros componentes esenciales para su

funcionamiento.

## Soporte Motor

1

## Esta pieza se encargará de sostener y brindar apoyo al motor, cuyo eje estará conectado al disco de rodamiento. Este diseño permitirá la conexión de los pines de salida, que emitirán señales indicando la presencia de

movimiento.

41

## Hoja Grande en L

6

Es una hoja fija que no se mueve.

## Está diseñada para formar parte de la estructura estática del demostrador, contribuyendo a la estabilidad y el equilibrio del

sistema en su conjunto.

## Hoja Pequeño en L 6

Es una hoja fija que no se mueve,

## de menor tamaño que la pieza anterior. Está diseñada para formar parte de la estructura

estática del demostrador,

## contribuyendo a la estabilidad y el equilibrio del sistema en su

conjunto.

## Pala Cuadrada

8

## Es una de las palas móviles clave que gira cuando es impulsada por el viento. Su diseño cuadrado permite capturar eficientemente la energía cinética del viento y convertirla en movimiento

rotatorio.

## Disco grande 2

## Es un componente clave que actúa como soporte estructural para las palas móviles. Este disco está diseñado para girar cuando

las palas capturan el viento,

## transfiriendo el movimiento rotatorio hacia el eje central del

sistema.

## Disco

Pequeño | 3

## Es un componente estático que no se mueve. Su función principal es actuar como parte del soporte

estructural del dispositivo,

## ayudando a mantener la correcta alineación y estabilidad

42

## de los elementos móviles, como

las hojas y los discos grandes.

## Disco rodamiento 1

## Es un componente crucial que se utiliza para reducir la fricción entre las partes móviles del sistema. Este disco actúa como un soporte rotatorio que permite que los componentes, como el Disco Grande y las palas, giren de manera suave y eficiente

alrededor del eje central.

Tapa | 1

## Es un componente estructural que se coloca en la parte

superior del conjunto,

## asegurando que todos los elementos internos estén protegidos y correctamente

alineados.

## Rodamiento 1

## Es un componente mecánico que permite que los elementos giratorios, como los discos y las palas, se muevan con mínima

fricción.

Espigas Madera | 3

## Es un componente estructural utilizado para conectar y asegurar las diferentes piezas de

madera del dispositivo.

# A continuación se muestra cómo se realiza el montaje del demostrador:

Nota: Es necesario insertar el engranaje de 10 dientes en el eje del motor DC antes de comenzar con el montaje del demostrador.

43


44


45

46


47


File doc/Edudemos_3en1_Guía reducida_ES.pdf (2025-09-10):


# EDUDEMOS

# Financiado por la Unión Europea. Las opiniones y puntos de vista expresados solo comprometen a su(s) autor(es) y no reflejan necesariamente los de la Unión Europea o los de la Agencia Ejecutiva Europea de Educación y Cultura (EACEA). Ni la Unión Europea ni la EACEA

pueden ser considerados responsables de ellos.

EduDemoS 3in1 © 2025 by Gerda Stetter Stiftung – Technik macht Spaß!,

# Sergio Alonso Fundation, FINNOVA REGIO, GBS St. Gallen e IES El Rincón is licensed under

# Creative Commons Attribution-NonCommercial-ShareAlike 4.0 International. To view a copy of this license, visit https://creativecommons.org/licenses/by-nc-sa/4.0/

1

Financiado por la Unión Europea. Las opiniones y puntos de vista expresados solo comprometen a su(s) autor(es) y no reflejan necesariamente los de la Unión Europea o los de la Agencia Ejecutiva Europea de Educación y Cultura (EACEA). Ni la Unión Europea ni la EACEA pueden ser considerados responsables de ellos.

# 1. ENSAMBLAJE DEL DEMOSTRADOR 3x1

El montaje del Demostrador 3x1 se realizará de forma modular, abordando cada sección por separado en los apartados correspondientes de esta guía. Este enfoque busca simplificar el proceso y facilitar su comprensión, permitiendo que el montaje sea claro y accesible para quienes lo lleven a cabo. Cada paso está diseñado con el objetivo de garantizar un resultado funcional y efectivo, incluso para quienes no cuenten con

experiencia previa en ensamblaje de demostradores.

Uno de los objetivos principales de este proyecto es fomentar la autonomía de los centros educativos, permitiéndoles crear sus propios demostradores si cuentan con impresoras 3D en sus instalaciones. Por esta razón, hemos puesto a disposición los archivos de impresión necesarios para la fabricación de los componentes, los cuales

pueden descargarse a través del siguiente enlace: Archivos de impresión 3D. (https://drive.google.com/drive/folders/1F19XPgi768G87Ds_K66nvXBx-3E4KJT6) Con esta

# herramienta, buscamos empoderar a las instituciones educativas para que integren

estos demostradores en sus actividades de forma independiente y eficiente.

# 1. 1. Listado de materiales

- 1 x ESP32 DEVKIT V1 de 30 pines - 2 x Mini breadboard de 170 puntos - 1 x Módulo DHT11, de ancho máximo 14 mm y puede o no tener led incluido - 10/12* x Cables macho-macho 10 cm - 5 x Cables macho-macho 20 cm - 3 x Cables macho-hembra 10 cm - 10 x Cables macho-hembra 20 cm - 5 x Resistencias de 1k ohmio - 1 x Condensador de 100nF / 1uF - 3 x Leds de colores (Rojo, Verde y Azul preferiblemente) - 1 x Placa solar dimensiones máximas: 45 mm x 60 mm - 1 x Sensor nivel de agua, 6 cm x 2 cm - 1 x Motor DC de corriente continua de 5V, dimensiones máximas: 28 mm - diámetro y 45 mm largo - 1 x Servomotor SG-90

2

- 1 x Detector de tensión - 2 x Fotoresistencias independientes GL5528 - 1 x Rodamiento 6203 puede ser del tipo zz o 2rs: 40 mm diámetro exterior, 17 - mm diámetro interior y 12 mm de alto - 3 x Espiga de madera: 8 mm de diámetro y 40mm de largo - 1 x Engranaje motor: 2 mm diámetro interior, 10 dientes y 5 mm alto - 1 x Cable de datos USB a microUSB - 1 x Cinta adhesiva de aluminio, 5 cm de ancho - 1 x Cinta adhesiva de doble cara, 3 cm de ancho

# * Si el Motor DC no viene con los cables soldados, se necesitarán 12 cables macho-

macho de 10 cm.

# Herramientas que podrías necesitar:

- Soldador: si el motor DC o el panel solar no vienen con cables.
- Destornillador plano de 2 mm: para el sensor de voltaje.

# 1. 2. Montaje del Demostrador de Agua + Solar

# 1. 2. 1. Montaje electrónico (Parte de Agua)

# Comenzaremos realizando el montaje del captador de agua. Para realizar este montaje completo necesitarás el siguiente material:


1 x Sensor DHT-11 | 3 x Resistencias de 1 kΩ

3

# Encargado de medir la temperatura y

la humedad ambientales.

# Usadas para limitar la corriente que

fluye por los diodos LED.

# 3 x LEDs de Colores (Rojo, Verde y Azul preferiblemente)

# 1 x Cable dupont (Macho-Macho) 10cm

# Empleados como indicadores visuales

del rango de la temperatura medida.

# Necesarios para realizar las conexiones entre los diferentes componentes en la

protoboard.

# 2 x Mini Breadboard

# 6 x Cable dupont (Macho-Hembra) 20cm

# Componente necesario para conectar la placa microcontroladora con los diferentes componentes

# Necesarios para realizar las conexiones entre los diferentes componentes en la

protoboard.

4

1 x Sensor nivel de agua | 1 x ESP32 DEVKIT V1 (30 pins)
Empleado para medir el nivel de agua en el tanque. | Encargado de ejecutar la programación que controla el funcionamiento de la electrónica.

El objetivo del montaje será obtener el valor de la temperatura y la humedad ambientales y, en función del valor de la temperatura, encender un LED u otro como indicadores de peligro por alta o baja temperatura. De esta manera si la temperatura está por debajo de los 20ºC se enciende el LED Azul, si se está por encima de los 25ºC se enciende el LED Rojo y si está entre ambos valores (entre 20 y 25ºC) se enciende el LED

Verde.

# El primer paso es colocar la placa con ESP32 sobre dos protoboard pequeñas para tener espacio suficiente para luego conectar los componentes que vamos a necesitar. A continuación se puede ver el resultado:

5


# Una vez tengamos el microcontrolador colocado en las dos protoboards, empezaremos a conectar los LEDs de colores con sus resistencias limitadoras. Vamos a empezar

colocando el LED Azul y una de las resistencias de 1 kΩ en serie. Conectaremos el positivo

# del LED en el pin D5, y utilizaremos cualquier pin GND para conectar el negativo del

circuito. A continuación se puede ver el montaje indicado.

Nota: El diodo LED nos indica la polaridad de la conexión a simple vista con el tamaño de sus patas de conexión. La más larga coincide con el ánodo, o positivo, y la más corta se trata del cátodo, o negativo. En el diagrama, la pata larga es la que va conectada en serie con la resistencia.

6


# Para comprobar el correcto funcionamiento del montaje, podemos cargar el siguiente código en el ESP32:

#define ledPin1Cold 5 // Definimos el pin donde está conectado el LED Azul

// Bloque de inicialización

void setup() {

// Configuramos el modo de funcionamiento del pin del LED como salida

pinMode(ledPin1Cold, OUTPUT);

}

// Bucle principal del código

void loop() {

digitalWrite(ledPin1Cold, LOW); // Apagamos el LED

delay(1000); // Esperamos 1 segundo = 1000 milisegundos

digitalWrite(ledPin1Cold, HIGH); // Encendemos el LED

delay(1000); // Esperamos 1 segundo

7

}

# Este pequeño programa hace parpadear el LED Azul, cambiando su estado entre encendido y apagado cada segundo. Si no funciona correctamente, comprueba que el

LED se encuentre bien orientado (recuerda que el terminal más largo es el positivo,

# mientras el corto es el negativo) y conectado adecuadamente con la resistencia

limitadora.

# El siguiente paso del montaje será añadir un segundo LED. Esta vez colocaremos y conectaremos el LED de color Verde en el pin D18 con su resistencia. Puedes ver el

esquema de montaje indicado en la siguiente imagen.


# Vamos a comprobar de nuevo que el montaje es correcto. Vamos a utilizar ahora el código que encontrarás a continuación para verificar que el nuevo LED también está

adecuadamente colocado.

8

#define ledPin1Cold 5 // Definimos el pin donde está conectado el LED Azul

#define ledPin2Good 18 // Definimos el pin donde está conectado el LED Verde

// Bloque de inicialización

void setup() {

// Configuramos el modo de funcionamiento de los pines de los LED como salida

pinMode(ledPin1Cold, OUTPUT);

pinMode(ledPin2Good, OUTPUT);

}

// Bucle principal del código

void loop() {

digitalWrite(ledPin1Cold, LOW); // Apagamos el LED Azul

digitalWrite(ledPin2Good, LOW); // Apagamos el LED Verde

delay(1000); // Esperamos 1 segundo = 1000 milisegundos

digitalWrite(ledPin1Cold, HIGH); // Encendemos el LED Azul

digitalWrite(ledPin2Good, HIGH); // Encendemos el LED Verde

delay(1000); // Esperamos 1 segundo

}

Como puedes ver, el objetivo del código es el mismo: encender y apagar, esta vez,

# ambos LED cambiando de estado cada segundo. Si el LED Azul y el Verde cambian de estado correctamente, podemos dar por válido el montaje actual y continuar con el

siguiente paso.

# Para terminar de montar los LEDs de colores que necesitamos para cumplir con el objetivo establecido con esta parte del Demostrador, necesitamos conectar el último LED de color Rojo en el pin D19. Procede a montar el diodo LED y la última resistencia

correspondiente, como se muestra en la siguiente imagen.

9


# Comprobaremos que está correcto realizando la misma programación que en los casos

anteriores, generando un parpadeo, ahora, en los tres LEDs de colores. El código para ello es el que sigue.

#define ledPin1Cold 5 // Definimos el pin donde está conectado el LED Azul

#define ledPin2Good 18 // Definimos el pin donde está conectado el LED Verde

#define ledPin3Heat 19 // Definimos el pin donde está conectado el LED Rojo

// Bloque de inicialización

void setup() {

// Configuramos el modo de funcionamiento de los pines de los LED como salida

pinMode(ledPin1Cold, OUTPUT);

pinMode(ledPin2Good, OUTPUT);

pinMode(ledPin3Heat, OUTPUT);

}

// Bucle principal del código

void loop() {

10

digitalWrite(ledPin1Cold, LOW); // Apagamos el LED Azul

digitalWrite(ledPin2Good, LOW); // Apagamos el LED Verde

digitalWrite(ledPin3Heat, LOW); // Apagamos el LED Rojo

delay(1000); // Esperamos 1 segundo = 1000 milisegundos

digitalWrite(ledPin1Cold, HIGH); // Encendemos el LED Azul

digitalWrite(ledPin2Good, HIGH); // Encendemos el LED Verde

digitalWrite(ledPin3Heat, HIGH); // Encendemos el LED Rojo

delay(1000); // Esperamos 1 segundo

}

# El próximo paso es agregar y conectar el sensor DHT11 en el pin D32, ya sea como un componente individual o en un módulo. A continuación se presenta el montaje realizado

hasta este momento junto con las conexiones del sensor DHT11.


11
Nota: Comprobar que las conexiones GND y VCC del sensor DHT11 se corresponden con la descripción de los pines reales del componente, ya que puede ser diferente a la que aparece en el diagrama.

Pasamos a comprobar el correcto funcionamiento del sensor DHT-11. A continuación,

dispones de un código de prueba de todo el montaje realizado para esta parte del montaje. Carga el programa y verás cómo, además de que los LEDs de colores parpadean como han hecho hasta ahora, la placa con ESP32 enviará por el Monitor Serial (puedes ver el botón donde abrirlo en la siguiente imagen) cada par de segundos las medidas obtenidas de temperatura ambiental (en ºC) y humedad relativa del aire

(en %).

#include <DHT.h> // Incluimos la librería necesaria para controlar de DHT

#define ledPin1Cold 5 // Definimos el pin donde está conectado el LED Azul

#define ledPin2Good 18 // Definimos el pin donde está conectado el LED Verde

#define ledPin3Heat 19 // Definimos el pin donde está conectado el LED Rojo

#define DHTPIN 32 // Definimos el pin donde está conectado el DHT

#define DHTTYPE DHT11 // Definimos el tipo de sensor DHT que vamos a utilizar

// Creamos un objeto de tipo DHT con la configuración correspondiente

DHT myDHT11(DHTPIN, DHTTYPE);

// Bloque de inicialización

void setup() {

// Configuramos el modo de funcionamiento de los pines de los LED como salida

12

pinMode(ledPin1Cold, OUTPUT);

pinMode(ledPin2Good, OUTPUT);

pinMode(ledPin3Heat, OUTPUT);

// Inicializamos el monitor Serial

Serial.begin(115200);

// Inicializamos el sensor DHT

myDHT11.begin();

}

// Bucle principal del código

void loop() {

digitalWrite(ledPin1Cold, LOW); // Apagamos el LED Azul

digitalWrite(ledPin2Good, LOW); // Apagamos el LED Verde

digitalWrite(ledPin3Heat, LOW); // Apagamos el LED Rojo

delay(1000); // Esperamos 1 segundo = 1000 milisegundos

digitalWrite(ledPin1Cold, HIGH); // Encendemos el LED Azul

digitalWrite(ledPin2Good, HIGH); // Encendemos el LED Verde

digitalWrite(ledPin3Heat, HIGH); // Encendemos el LED Rojo

delay(1000); // Esperamos 1 segundo

//Obtenemos las medidas del sensor DHT

float temperatura = myDHT11.readTemperature();

float humedad = myDHT11.readHumidity();

// Mostramos los valores por monitor Serial

Serial.print("Temperatura: ");

Serial.println(temperatura);

Serial.print("Humedad: ");

Serial.println(humedad);

}

# Con el monitor abierto, comprueba que el desplegable que se ubica más a la derecha sobre el propio Monitor tenga seleccionado el valor “115200”. Ahora podrás ver los datos que envía el ESP32 tomados del DHT-11 de manera constante y verificar que el montaje

hasta este punto funciona correctamente.

13

# El siguiente componente que se va a añadir va a ser el módulo de sensor de nivel de agua. Conectamos el sensor en el pin VN. En la siguiente imagen se ve como quedaría el montaje:


# Ahora vamos a verificar el funcionamiento del sensor de nivel de agua leyendo y mostrando por el monitor serial constantemente el valor medido del sensor:

//Water sensor calibration

const int WaterSensorPin = 39; // Analog Value from VN PIN

void setup() {

Serial.begin(115200);

}

void loop() {

int sensorValue; // Variable to store sensor values

sensorValue = analogRead(WaterSensorPin); // Read the value from the sensor

Serial.println(sensorValue); // Print value in serial monitor

delay(100);

14

}

15

# 1. 2. 2. Montaje electrónico (Parte Solar)

# Comenzaremos realizando el montaje del componente solar. Para realizar este montaje completo necesitarás el siguiente material:

# 1 x Servomotor SG-90

# 2 x Fotoresistencias independientes

# Utilizado para mover el Demostrador

solar y orientarlo hacia la luz solar.

# Empleados para medir el nivel de

luminosidad recibida.

# 2 x Resistencias 1k ohm

# 9 x Cable dupont (Macho-Macho) 10cm

# Utilizadas solamente junto con las LDR independientes para montar un partidor de tensión controlado por

intensidad lumínica.

# Necesarios para realizar las conexiones entre los diferentes componentes en la

protoboard.

16

# 5 x Cable dupont (Macho-Macho) 20cm

# 3 x Cable dupont (Macho-Hembra) 10cm

# Necesarios para realizar las conexiones entre los diferentes componentes en la

protoboard.

# Necesarios para realizar las conexiones entre los diferentes componentes en la

protoboard.

# 4 x Cable dupont (Macho-Hembra) 20cm

# 1 x Detector de tensión

# Necesarios para realizar las conexiones entre los diferentes componentes en la

protoboard.

# Necesarios para realizar las conexiones entre los diferentes componentes en la

protoboard.

# 1 x Panel solar

17
Empleado para detectar luz solar. El objetivo del montaje será obtener la orientación de la incidencia de la luz solar con las

# LDR y rotar el Demostrador para que incida la mayor cantidad de rayos solares sobre el

panel.

# El montaje del componente solar va a comenzar desde el último montaje que se vio en

el apartado anterior. En este montaje se añade una LDR y una resistencia en serie,

# formando un partidor de tensión controlado por la intensidad lumínica. Para obtener el

valor del sensor se va a utilizar la salida digital del mismo, que se va a conectar al pin

# D34 del ESP32. El montaje se puede ver a continuación:


18
Para comprobar el funcionamiento de los nuevos elementos añadidos al montaje,

# vamos a emplear un código que solamente tome la medida de la LDR para encender el LED Rojo con mayor o menor intensidad según la luminosidad medida por la

fotorresistencia. Puedes ver el código a cargar a continuación.

#define ldrPin1 34 // Definimos el pin donde está conectado la LDR

// Bloque de inicialización

void setup() {

// Inicializamos el monitor serial

Serial.begin(115200);

}

// Bucle principal del código

void loop() {

// Tomamos la lectura del pin donde se encuentra la LDR

int lectura_ldr_1 = analogRead(ldrPin1);

// Mostramos el valor por el monitor Serial

Serial.print("Luminosidad 1: ");

Serial.println(lectura_ldr_1);

}

# A continuación se debe añadir la segunda LDR con su resistencia. Para obtener el valor

de la lectura de este sensor se va a utilizar la salida digital, como en el caso anterior,

# pero esta se va a conectar al pin D35. A continuación se puede ver el montaje con

ambas LDR para la parte actual del Demostrador.

19


Comprobemos que se ha conectado correctamente empleando el siguiente código,

# que es muy similar al anterior pero mostrando el valor de la medida de ambas

fotorresistencias.

#define ldrPin1 34 // Definimos el pin donde está conectado la primera LDR

#define ldrPin2 35 // Definimos el pin donde está conectado la segunda LDR

// Bloque de inicialización

void setup() {

// Inicializamos el monitor serial

Serial.begin(115200);

}

20

// Bucle principal del código

void loop() {

// Tomamos las lecturas de los pines donde se encuentran las LDR

int lectura_ldr_1 = analogRead(ldrPin1);

int lectura_ldr_2 = analogRead(ldrPin2);

// Mostramos el primer valor por el monitor Serial

Serial.print("Luminosidad 1: ");

Serial.println(lectura_ldr_1);

// Mostramos el segundo valor por el monitor Serial

Serial.print("Luminosidad 2: ");

Serial.println(lectura_ldr_2);

}

# El siguiente componente que se va a añadir en el montaje es un servomotor. Este se va a conectar a ambas lineas de alimentación (cable rojo a la positiva y cable negro a la

negativa) y el cable amarillo (que es la señal de control) se va a conectar al pin D25.


21

# Comprobaremos el funcionamiento del servomotor cargando el siguiente código en la placa ESP32 que realiza un barrido moviendo el servo entre las posiciones de 0º, 90º y

180º, en bucle, una y otra vez.

#include <ESP32Servo.h> // Incluir la librería necesaria para controlar el servomotor

#define servoPin 25 // Definimos el pin donde está conectado el servomotor

// Creamos un objeto de tipo Servo para controlarlo

Servo myServo;

// Bloque de inicialización

void setup() {

// Asociamos el servo que creamos al pin donde está conectado

myServo.attach(servoPin);

// Colocamos el servo en una posición inicial de 0º

myServo.write(0);

}

// Bucle principal del código

void loop() {

myServo.write(0); // Movemos el servomotor a 0º

delay(1000); // Esperamos 1 segundo = 1000 milisegundos

myServo.write(90); // Movemos el servomotor a 90º

delay(1000); // Esperamos 1 segundo

myServo.write(180); // Movemos el servomotor a 180º

delay(1000); // Esperamos 1 segundo

}

Nota: Colocar la pestaña en el servo. No es necesario usar tornillos para sujetarla.

# El último componente que vamos a conectar al ESP32 será un detector de tensión. Este módulo se debe alimentar a ambas líneas de alimentación (Vcc y GND). La línea de

señal se va a conectar al pin VP.

22


# El último paso que falta para terminar el montaje electrónico es conectar el panel solar

al detector de tensión. A continuación se puede ver cómo quedaría el montaje completo.

23

# Vamos a comprobar el funcionamiento del detector solar completo haciendo uso del siguiente código que simplemente lee la señal del módulo detector de tensión y

enciende el LED Azul si detecta voltaje.

#define ledPin1Cold 5 // Definimos el pin donde está conectado el LED Azul

#define detectorPin 36 // Definimos el pin donde está conectado el Detector de Tensión

// Bloque de inicialización

void setup() {

// Configuramos el modo de funcionamiento del pin del LED como salida

pinMode(ledPin1Cold, OUTPUT);

}

// Bucle principal del código

void loop() {

// Tomamos la lectura del Módulo Detector

bool tension_detectada = digitalRead(detectorPin);

// Comprobamos si hay tensión o no

if(tension_detectada) { // Sí hay tensión

digitalWrite(ledPin1Cold, HIGH); // Encendemos el LED Azul

} else { // No hay tensión

digitalWrite(ledPin1Cold, LOW); // Apagamos el LED Azul

}

}

# A continuación, dejamos un código test para comprobar que todos los sensores

obtienen | lecturas | y | funcionan | correctamente:

//include the necessary libraries
#include <ESP32Servo.h>

#include "DHT.h"

// Pin definitions and constants

#define ldrPin1 34 // set ldr 1 Analog input pin of East ldr as an integer

24

#define ldrPin2 35 // set ldr 2 Analog input pin of West ldr as an integer

#define DHTPIN 32

#define DHTTYPE DHT11

#define ledPin1Cold 5

#define ledPin2Good 18

#define ledPin3Heat 19

#define SolarPin 36

// Global variables

DHT dht(DHTPIN, DHTTYPE);

Servo myservo;

int valldr1 = 0 ;

int valldr2 = 0 ;

int averageLdrValue = 0;

int servopos = 90; // initial position of the Horizontal movement controlling servo motor

int tolerance = 20; // allowable tolerance setting - so solar servo motor isn't constantly

in motion

float lastMicrovolts = 0;

const int WaterSensorPin = 39; // Analog Value from VN PIN

int sensorValue; // Variable to store sensor values

void setup(){

Serial.begin(115200);

analogReadResolution(12); // ESP32 has a 12-bit ADC

analogSetAttenuation(ADC_11db); // Set attenuation for higher sensitivity

pinMode(4, INPUT);

dht.begin(); // Start the DHT sensor

pinMode(ledPin1Cold, OUTPUT);

pinMode(ledPin2Good, OUTPUT);

pinMode(ledPin3Heat, OUTPUT);

myservo.attach(25); // attaches the servo on digital pin 2 to the horizontal movement servo

motor

pinMode(ldrPin1, INPUT); //set East ldr pin as an input

pinMode(ldrPin2, INPUT); //set West ldr pin as an input

myservo.write(servopos); // write the starting position of the horizontal movement servo

motor

delay(1000); // 1 second delay to allow the solar panel to move to its staring position

before commencing solar tracking

25

}

void loop(){

Serial.println("----------------------------- Measured Solar (V) ----------------------

------ ");

int solarVoltagedV = analogRead ( SolarPin); //dV

int solarVoltage = solarVoltagedV * 10;

Serial.print("Voltage of Solar Panel: ");

Serial.println(solarVoltage);

// Calculate voltage

float voltage = (solarVoltage / 4095.0) * 3.3; // For 12-bit ADC (0-4095)

Serial.print("Measured voltage (V): ");

Serial.println(voltage); // Display the measured voltage

// Convert to microvolts

float microvoltsSolar = voltage * 1000000.0;

Serial.print("Input voltage (µV): ");

Serial.println(microvoltsSolar);

// Apply a minimum threshold to filter noise

const float threshold = 10.0; // Threshold in microvolts

if (microvoltsSolar < threshold) {

microvoltsSolar = 0;

}

// Check if the microvolts value has changed

if (microvoltsSolar != lastMicrovolts) {

Serial.print("Send voltage: ");

Serial.print(microvoltsSolar, 2); // Display with 2 decimal places

Serial.println(" µV");

// Update the last microvolts value

lastMicrovolts = microvoltsSolar;

}

Serial.println("----------------------- Measured Temperature / Humidity ---------------

-------- ");

// Read values from DHT sensor

float h = dht.readHumidity();

float t = dht.readTemperature();

26

// Check if readings are valid

if (isnan(h) || isnan(t)) {

Serial.println("Failed to read from DHT sensor!");

return;

}

// Print sensor values

Serial.print("Temperature: ");

Serial.print(t);

Serial.print(" °C, Humidity: ");

Serial.print(h);

Serial.print(" %");

// Example LED control based on temperature

if (t < 20) {

digitalWrite(ledPin1Cold, HIGH);

digitalWrite(ledPin2Good, LOW);

digitalWrite(ledPin3Heat, LOW);

Serial.println("Cold is HIGH");

} else if (t >= 20 && t < 25) {

digitalWrite(ledPin1Cold, LOW);

digitalWrite(ledPin2Good, HIGH);

digitalWrite(ledPin3Heat, LOW);

Serial.println("Good is HIGH");

} else {

digitalWrite(ledPin1Cold, LOW);

digitalWrite(ledPin2Good, LOW);

digitalWrite(ledPin3Heat, HIGH);

Serial.println("Heat is HIGH");

}

Serial.println("----------------------------- Measured Water Level --------------------

--------- ");

int sensorValue; // Variable to store sensor values

sensorValue = analogRead(WaterSensorPin); // Read the value from the soil moisture sensor

//Check watersensor calibration first

if (sensorValue >= 2000) { //These value represents de max value given

sensorValue = 1980; //This value would return a 99% value

}

float waterlevel = (sensorValue*100)/2000 ; //Calculation to return the %

27

Serial.print("Water level: "); // Print value in serial monitor

Serial.print(waterlevel); // Print value in serial monitor

Serial.println(" %"); // Print value in serial monitor

Serial.println("----------------------------- Measured LDR and Servo ------------------

----------- ");

// Read LDR values

valldr1 = analogRead(ldrPin1); // read the value of ldr 1

valldr2 = analogRead(ldrPin2); // read the value of ldr 2

// Invert readings so low values mean darkness and high values mean light

averageLdrValue = (valldr1 + valldr2) / 2;

// Print readings for debugging

Serial.print("LDR 1: ");

Serial.print(valldr1);

Serial.print(" | LDR 2: ");

Serial.println(valldr2);

Serial.print("Average LDR: ");

Serial.println(averageLdrValue);

if((abs(valldr1 - valldr2) <= tolerance) || (abs(valldr2 - valldr1) <= tolerance)) {

//no servo motor horizontal movement will take place if the ldr value is within the

allowable tolerance

}else {

if(valldr1 > valldr2) // if ldr1 senses more light than ldr2

{

servopos = servopos+10; // decrement the 90 degree position of the horizontal servo motor

- this will move the panel position Eastward

}

if(valldr1 < valldr2) // if ldr2 senses more light than ldr1

{

servopos = servopos-10; // increment the 90 degree position of the horizontal motor - this

will move the panel position Westward

}

}

if(servopos > 180) {servopos = 180;} // reset the horizontal position of the motor to 180

if it tries to move past this point

if(servopos < 0) {servopos = 0;} // reset the horizontal position of the motor to 0 if it

tries to move past this point

myservo.write(servopos); // write the starting position to the horizontal motor

28

// Print the servo angle

Serial.print("Servo angle: ");

Serial.print(servopos);

delay(5000);

}

29

# 1. 2. 3. Montaje Mecánico del Demostrador de Agua + Solar

# Los elementos que componen este demostrador son los siguientes:

Elemento | Cantidad | Descripción | Imagen
Base | 1

## Es la parte superior que asegura los componentes móviles, como

las palas y el eje del motor.

## Proporciona estabilidad y permite que el sistema funcione suavemente, facilitando la correcta transferencia de energía desde las palas al

generador.

Cajón | 1

## Es la base que conecta las diferentes secciones del dispositivo, proporcionando soporte estructural y asegurando una correcta alineación entre el motor, las palas y otros componentes esenciales para su

funcionamiento.

## Contenedor de agua

1

## Esta parte es capaz de almacenar el agua que cae en

él.

Hoja | 8

## Hoja que permite que los líquidos entren en el contenedor de agua

30

## Disco

Pequeño | 3

## Es un componente estático que no se mueve. Su función principal es actuar como parte del soporte

estructural del dispositivo,

## ayudando a mantener la correcta alineación y estabilidad

de los elementos.

## Disco

Estático | 2

## Disco que se mantiene fija para tapar y mantener la estabilidad

de la estructura.

Placa Sol | 1

## Parte que permite el movimiento del panel solar para su correcta orientación

Disco Solar | 1

## Disco que permite conectar el girador solar con un servomotor instalado y juntarlo con el resto

de la estructura.

# A continuación se muestra cómo se realiza el montaje del demostrador:

Nota: La cinta de aluminio se utiliza en la superficie de las hojas para optimizar la recolección de agua. La cinta de doble cara se utiliza en la parte trasera del panel solar para pegarlo en la pieza del “placa sol”.

El sensor de nivel de agua va colocado en unas ranuras dentro de la pieza “contenedor de agua”.

Al colocar los componentes electrónicos en el montaje mecánico, es necesario usar cables adicionales para alargar las conexiones de las LDR y de la placa solar.

31


32

33


34


35


36

# 1. 3. Montaje del Demostrador de viento

# 1. 3. 1. Montaje electrónico

# Comenzaremos realizando el montaje del Demostrador de viento. Para realizar este montaje completo necesitarás el siguiente material:

# 1 x Motor de Corriente Continua de 5V

# 1 x Condensador de 100nF / 1uF

# Empleado para generar voltaje con la

fuerza del viento.

# Utilizados para eliminar ruidos indeseados generados por el Motor de

CC.

# 2 x Resistencias de 1 kΩ

# 6 x Cable dupont (Macho-Macho) 10cm

# Utilizados en el divisor de tensión que permite tomar la lectura de tensión

generada por el Motor de CC.

# Necesarios para realizar las conexiones entre los diferentes componentes en la

protoboard.

37

2 x Mini Breadboard | Soldador de estaño
Componente necesario para conectar la placa microcontroladora con los diferentes componentes | sólo si el motor no tiene cables incluidos

# 1 x ESP32 DEVKIT V1 (30 pins)

# Encargado de ejecutar la programación que controla el funcionamiento de la

electrónica.

El objetivo del montaje será obtener la medida de la cantidad de voltaje generado por el motor, que irá unido a la estructura mecánica que girará por efecto de la fuerza del viento. Para poder realizar la medición con el ESP32 de la tensión obtenida por el movimiento de las aspas del Demostrador, debemos montar un partidor de tensión que

38

# reduzca el nivel máximo de tensión a obtener (5V) a uno que sea apto para el ESP32 (que trabaja a 3’3V). Con esto podremos obtener cuánto voltaje se está generando por

efecto del viento.
Para este nuevo montaje, será necesario crear un circuito desde el principio.

# Comenzaremos colocando el ESP32 en dos mini protoboards. A continuación, se muestra

el montaje correspondiente.


# A continuación, se procederá a montar un divisor de tensión. El punto intermedio de este divisor se conectará al pin D39 (VN). Además, es necesario conectar un condensador entre el terminal de este pin y GND, que servirá de filtro para las

variaciones indeseadas en la medida, tal y como se muestra en la imagen siguiente.

39


# El último paso en el montaje electrónico de este demostrador es conectar el motor al conjunto anterior, de manera que uno de sus terminales se une a GND y el otro terminal a la entrada del divisor de tensión montado antes. A continuación, se presenta este

montaje terminado.


40

# Vamos a comprobar que el montaje de este Demostrador funciona correctamente haciendo uso del siguiente fragmento de código en el que solamente leemos la salida del divisor de tensión que está unida al ESP32. Girando el rotor del motor, veremos como

la medición va dando diferentes valores a través del Monitor Serial.

// Bloque de inicialización

void setup() {

// Inicializamos el Monitor Serial

Serial.begin(115200);

}

// Bucle principal del código

void loop() {

// Tomamos la medida del pin que va a la salida del partidor de tensión

int medicion = analogRead(39);

// Mostramos la medida por el monitor serial

Serial.println(medicion);

}

41

# 1. 3. 2. Montaje Mecánico

# Los elementos que componen este demostrador son los siguientes:

Elemento | Cantidad | Descripción | Imagen
Base | 1

## Es la parte superior que asegura los componentes móviles, como

las palas y el eje del motor.

## Proporciona estabilidad y permite que el sistema funcione suavemente, facilitando la correcta transferencia de energía desde las palas al

generador.

Cajón | 1

## Es la base que conecta las diferentes secciones del dispositivo, proporcionando soporte estructural y asegurando una correcta alineación entre el motor, las palas y otros componentes esenciales para su

funcionamiento.

## Soporte Motor

1

## Esta pieza se encargará de sostener y brindar apoyo al motor, cuyo eje estará conectado al disco de rodamiento. Este diseño permitirá la conexión de los pines de salida, que emitirán señales indicando la presencia de

movimiento.

42

## Hoja Grande en L

6

Es una hoja fija que no se mueve.

## Está diseñada para formar parte de la estructura estática del demostrador, contribuyendo a la estabilidad y el equilibrio del

sistema en su conjunto.

## Hoja Pequeño en L 6

Es una hoja fija que no se mueve,

## de menor tamaño que la pieza anterior. Está diseñada para formar parte de la estructura

estática del demostrador,

## contribuyendo a la estabilidad y el equilibrio del sistema en su

conjunto.

## Pala Cuadrada

8

## Es una de las palas móviles clave que gira cuando es impulsada por el viento. Su diseño cuadrado permite capturar eficientemente la energía cinética del viento y convertirla en movimiento

rotatorio.

## Disco grande 2

## Es un componente clave que actúa como soporte estructural para las palas móviles. Este disco está diseñado para girar cuando

las palas capturan el viento,

## transfiriendo el movimiento rotatorio hacia el eje central del

sistema.

## Disco

Pequeño | 3

## Es un componente estático que no se mueve. Su función principal es actuar como parte del soporte

estructural del dispositivo,

## ayudando a mantener la correcta alineación y estabilidad

43

## de los elementos móviles, como

las hojas y los discos grandes.

## Disco rodamiento 1

## Es un componente crucial que se utiliza para reducir la fricción entre las partes móviles del sistema. Este disco actúa como un soporte rotatorio que permite que los componentes, como el Disco Grande y las palas, giren de manera suave y eficiente

alrededor del eje central.

Tapa | 1

## Es un componente estructural que se coloca en la parte

superior del conjunto,

## asegurando que todos los elementos internos estén protegidos y correctamente

alineados.

## Rodamiento 1

## Es un componente mecánico que permite que los elementos giratorios, como los discos y las palas, se muevan con mínima

fricción.

Espigas Madera | 3

## Es un componente estructural utilizado para conectar y asegurar las diferentes piezas de

madera del dispositivo.

# A continuación se muestra cómo se realiza el montaje del demostrador:

Nota: Es necesario insertar el engranaje de 10 dientes en el eje del motor DC antes de comenzar con el montaje del demostrador.

44


45


46


47

48


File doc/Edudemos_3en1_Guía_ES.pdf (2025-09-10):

## EDUDEMOS

Financiado por la Unión Europea. Las opiniones y puntos de vista expresados solo comprometen a su(s) autor(es) y no reflejan necesariamente los de la Unión Europea o los de la Agencia Ejecutiva Europea de Educación y Cultura (EACEA). Ni la Unión Europea ni la EACEA pueden ser considerados responsables de ellos.

EduDemoS 3in1 © 2025 by Gerda Stetter Stiftung – Technik macht Spaß!, Sergio Alonso Fundation, FINNOVA REGIO, GBS St. Gallen e IES El Rincón is licensed under
Creative Commons Attribution-NonCommercial-ShareAlike 4.0 International. To view a copy of this license, visit https://creativecommons.org/licenses/by-nc-sa/4.0/

1

Financiado por la Unión Europea. Las opiniones y puntos de vista expresados solo comprometen a su(s) autor(es) y no reflejan necesariamente los de la Unión Europea o los de la Agencia Ejecutiva Europea de Educación y Cultura (EACEA). Ni la Unión Europea ni la EACEA pueden ser considerados responsables de ellos.

1. INTRODUCCIÓN A EDUDEMOS | 4
1. 1. ¿Qué es EduDemos? | 4
1. 2. Objetivos | 4
1. 3. Metodología | 4
1. 4. Partners | 5
2. DEMOSTRADOR 3x1 | 6
2. 1. Descripción de los modelos | 6
2. 1. 1. Objetivos | 6
2. 1. 2. Competencias educativas | 7
2. 1. 3. Conceptos básicos | 9
3. PROGRAMACIÓN DE LOS DEMOSTRADORES | 12
3. 1. Requisitos mínimos | 12
3. 2. Librerías necesarias | 16
3. 3. Encontrar y descargar el código | 17
3. 4. Funcionamiento del código | 19
3. 5. Programación del microcontrolador | 31
4. INTRODUCCIÓN A ELECTRÓNICA | 32
4. 1. Ley de Ohm | 32
4. 2. Componentes electrónicos | 34
4. 2. 1. Componentes básicos | 34
4. 2. 2. Alimentación de un circuito | 38
4. 2. 3. Configuración de componentes en un circuito | 39
4. 2. 4. Sensores | 40
4. 2. 5. Actuadores | 42
4. 3. Protoboard | 43
4. 3. 1. Actividades con Protoboard | 45
4. 3. 2. Divisor de tensión | 47
4. 3. 3. Actividades con divisores de tensión | 48
5. ENSAMBLAJE DEL DEMOSTRADOR 3x1 | 49

2
5. 1. Listado de materiales | 50
5. 2. Montaje del Demostrador de Agua + Solar | 51
5. 2. 1. Montaje electrónico (Parte de Agua) | 51
5. 2. 2. Montaje electrónico (Parte Solar) | 62
5. 2. 3. Montaje Mecánico del Demostrador de Agua + Solar | 75
5. 3. Montaje del Demostrador de viento | 82
5. 3. 1. Montaje electrónico | 82
5. 3. 2. Montaje Mecánico | 86
6. DATOS DE LOS SENSORES | 94
6. 1. Puerto Serie | 94
6. 2. Adafruit IO | 97
7. OTA (Over-The-Air) UPDATES | 102
8. PROBLEMAS TÍPICOS | 103

3
Este primer bloque contendrá toda la información necesaria para entender el proyecto, su financiación, objetivos y participantes. Los apartados de este primer bloque de la guía serán:

## 1. INTRODUCCIÓN A EDUDEMOS

### 1. 1. ¿Qué es EduDemos?

EduDemos es un proyecto educativo que desarrolla demostradores sostenibles basados en energías renovables, como el agua, el sol y el aire. Estos demostradores son herramientas interactivas y replicables utilizadas para enseñar a jóvenes y profesores sobre sostenibilidad y competencias digitales, integrando el aprendizaje práctico con la conciencia ambiental.

### 1. 2. Objetivos

El proyecto EduDemos tiene como objetivo principal sensibilizar a las nuevas generaciones, tanto jóvenes como profesores, sobre la sostenibilidad mediante el uso de demostradores basados en energías renovables como el sol, el agua y el aire. Además, busca mejorar las competencias digitales en el ámbito educativo, proporcionando herramientas tecnológicas prácticas y replicables. Otro de sus propósitos es fomentar una red de colaboración entre educadores para el intercambio de conocimientos y experiencias prácticas, promoviendo la adopción de prácticas sostenibles y contribuyendo a un futuro más verde en Europa.

### 1. 3. Metodología

La metodología del proyecto EduDemos se estructura en torno a la implementación práctica de demostradores sostenibles que utilizan fuentes de energía renovable como el agua, el sol y el aire. Estos demostradores no son solo herramientas teóricas; están diseñados para ser construidos y experimentados por los estudiantes, fomentando un aprendizaje activo y práctico.

4

- Desarrollo de modelos: Se diseñan modelos de demostradores que integran tecnologías de energías renovables. Estos modelos sirven como ejemplos prácticos que los estudiantes pueden replicar.
- Guías de construcción: EduDemos proporciona guías detalladas para la construcción de estos demostradores, asegurando que los estudiantes y docentes puedan seguir paso a paso el proceso. Estas guías son accesibles y están diseñadas para ser usadas en un entorno educativo, facilitando el aprendizaje de conceptos técnicos y científicos de manera práctica.
- Formación de docentes y estudiantes: Se implementan programas de formación dirigidos tanto a profesores como a estudiantes. Estos programas están orientados a desarrollar competencias tanto en sostenibilidad como en habilidades digitales, preparando a los participantes para enfrentar los desafíos del cambio climático. La formación incluye talleres, cursos, y recursos educativos que complementan el aprendizaje teórico con la aplicación práctica.
- Colaboración europea: El proyecto fomenta la colaboración entre distintas instituciones educativas y organizaciones en Europa. Esta red de cooperación permite el intercambio de conocimientos, experiencias y recursos, enriqueciendo el proceso educativo. Los socios en el proyecto trabajan en conjunto para adaptar y mejorar los modelos y guías según las necesidades locales y regionales, promoviendo una educación más inclusiva y eficaz en toda Europa.

### 1. 4. Partners

El proyecto EduDemos cuenta con varios socios clave que aportan su experiencia y recursos para el éxito del proyecto:

- Gerda Stetter Stiftung (Alemania): Esta fundación se especializa en proyectos educativos y tecnológicos, enfocándose en el desarrollo

5
sostenible. Su participación asegura que los aspectos técnicos y pedagógicos del proyecto sean de alta calidad.
- Fundación Sergio Alonso (España): Una fundación que apoya iniciativas educativas y sociales, especialmente en Canarias. Su contribución es crucial para la implementación del proyecto en España y para asegurar su relevancia local.
- FINNOVAREGIO (Bélgica): Esta organización se enfoca en la innovación regional y el desarrollo sostenible. Su rol en EduDemos es clave para integrar el proyecto en redes europeas de innovación y sostenibilidad.
- GBS St.Gallen (Suiza): Esta institución educativa suiza aporta su experiencia en formación profesional y técnica, especialmente en el ámbito de las energías renovables. Participa en el desarrollo de los contenidos educativos y la metodología del proyecto.
- IES El Rincón (España): Un instituto de educación secundaria en Gran Canaria, España, que actúa como uno de los centros piloto donde se implementan y prueban los demostradores sostenibles del proyecto. Su participación es fundamental para ajustar el proyecto a las necesidades de los estudiantes y profesores.

Cada uno de estos socios aporta su experiencia específica, lo que permite que EduDemos sea un proyecto integral que aborda la educación en sostenibilidad desde diferentes perspectivas y en varios contextos europeos. La colaboración entre estos partners asegura que los recursos desarrollados sean diversos, accesibles y aplicables en distintos entornos educativos.

## 2. DEMOSTRADOR 3x1

### 2. 1. Descripción de los modelos

6
2. 1. 1. Objetivos

El objetivo de los demostradores es enseñar y concienciar a los estudiantes sobre cómo se genera energía a partir del viento, el sol y la captación de agua, promoviendo una comprensión práctica de las energías renovables y la importancia de la sostenibilidad medioambiental. Estos demostradores buscan involucrar a los estudiantes en la construcción y experimentación con tecnologías sostenibles, fomentando habilidades técnicas y competencias relacionadas con la sostenibilidad.

Estos demostradores están dirigidos principalmente a estudiantes de la etapa educativa de formación profesional, pero también pueden ser utilizados en el nivel de secundaria . Concretamente abarca desde la educación secundaria obligatoria hasta el bachillerato y formación profesional, donde los estudiantes ya tienen una base en ciencias y tecnología que les permite comprender y experimentar con conceptos más avanzados como la energía eólica o solar.

Su valor educativo radica en su capacidad para ofrecer una experiencia de aprendizaje práctico y contextualizado en torno a las energías renovables. A través de la construcción y el uso del Demostrador 3x1, los estudiantes desarrollan una comprensión más profunda de cómo se genera la energía a partir del viento, el sol y la captación de agua, además de fomentar habilidades técnicas, competencias digitales y un mayor compromiso con la sostenibilidad ambiental. Esto facilita el aprendizaje activo y el desarrollo de competencias clave en ciencia y tecnología.

2. 1. 2. Competencias educativas

Los demostradores facilitan el desarrollo de competencias clave en estudiantes que se encuentran realizando una formación profesional, especialmente los que están cursando estudios de familias profesionales técnicas, pero también para estudiantes de 1º a 4º de ESO. A través de su construcción y análisis los estudiantes adquieren habilidades esenciales para su desarrollo, además de fomentar el trabajo en equipo, aplicar la creatividad y el pensamiento crítico para resolver problemas, también comprenderán el impacto de las tecnologías sostenibles en la sociedad.

7
Este enfoque fomenta una formación integral que prepara a los estudiantes para los desafíos actuales y futuros.

Competencias educativas a adquirir con el Demostrador 3x1 para 1º ESO - 4º ESO:

### 1. Competencia en comunicación lingüística (CCL):

Desarrollo de habilidades de comunicación: Los estudiantes aprenderán a comunicar sus ideas y resultados de manera efectiva en diferentes formatos (oral, escrito, visual), empleando un lenguaje técnico adecuado y respetuoso. Esto se aplica tanto en la representación de soluciones tecnológicas como en la elaboración de documentación técnica básica.

### 2. Competencia matemática y en ciencia, tecnología e ingeniería (STEM):

Diseño y fabricación de soluciones: Los estudiantes aplicarán conocimientos de matemáticas, ciencia y tecnología para diseñar y construir el Demostrador 3x1, utilizando herramientas de diseño asistido por ordenador y técnicas de fabricación digital.

### 3. Competencia digital (CD):

Uso de herramientas digitales: Los estudiantes emplearán aplicaciones y plataformas digitales para gestionar el proyecto, desde la ideación hasta la presentación final. Los estudiantes aprenderán a utilizar aplicaciones digitales para representar esquemas, circuitos y diseñar componentes del Demostrador 3x1.

### 4. Competencia personal, social y de aprender a aprender (CPSAA):

Trabajo en equipo y gestión de proyectos: A lo largo del proyecto, se fomentará la capacidad de los estudiantes para trabajar en equipo de manera efectiva, compartiendo responsabilidades y colaborando para resolver problemas. También se promoverá la autorreflexión y la mejora continua del proceso de aprendizaje mediante la evaluación crítica de las soluciones propuestas.

### 5. Competencia emprendedora (CE):

8
Creatividad e innovación: Los estudiantes serán desafiados a desarrollar soluciones tecnológicas innovadoras que generen valor para la comunidad, utilizando estrategias de resolución de problemas y fomentando un espíritu emprendedor. La planificación y ejecución de proyectos sostenibles y accesibles serán clave en este proceso.

### 6. Competencia en conciencia y expresión culturales (CCEC):

Valorización cultural y tecnológica: Los estudiantes aprenderán a expresar y difundir sus propuestas tecnológicas de manera creativa y efectiva, utilizando diversos medios y técnicas, y reflexionarán sobre la importancia de las tecnologías sostenibles en diferentes contextos culturales, reconociendo el valor del patrimonio tecnológico y su impacto en la sociedad.

Estas competencias se adquieren a través de un enfoque práctico y contextualizado en torno al Demostrador 3x1, para que los estudiantes no solo adquieran conocimientos técnicos, sino también habilidades transversales y una mentalidad crítica y sostenible, que son relevantes tanto en su vida académica como personal.

De esta manera, se contribuye ampliamente a las competencias establecidas en el Perfil de salida del alumnado al término de la enseñanza básica, favoreciendo la transversalidad del aprendizaje del alumnado, y la concreción de los principios y fines del sistema educativo español en este periodo educativo.

2. 1. 3. Conceptos básicos
- Demostrador de viento

El demostrador de viento es una herramienta educativa que permite a los estudiantes construir un pequeño aerogenerador para comprender los principios básicos de la energía eólica y su aplicación en la generación de electricidad. A través de la interacción con el dispositivo, los estudiantes aprenden cómo la energía cinética del viento se transforma primero en energía mecánica, mediante el movimiento de las palas, y luego en energía eléctrica gracias a un generador.

9

Este demostrador incluye componentes esenciales como palas, un eje y un generador, lo que facilita la comprensión práctica de conceptos como la aerodinámica de las palas, la relación entre la velocidad del viento y la eficiencia energética, y el impacto ambiental de la energía eólica frente a otras fuentes de energía. Además, permite explorar cómo el diseño y la orientación de las palas influyen en la maximización de la generación de energía.

Inspirado en los "Juguetes del Viento" de César Manrique, este dispositivo fusiona arte y funcionalidad educativa, conectando la herencia cultural de Canarias con la enseñanza de las energías renovables. Es una herramienta que no solo fomenta el aprendizaje técnico, sino que también celebra la armonía entre naturaleza, tecnología y cultura local.

- Demostrador solar

El demostrador solar es una herramienta educativa diseñada para que los estudiantes comprendan cómo la luz solar se convierte en electricidad mediante paneles fotovoltaicos. Inspirado en el movimiento de los girasoles, que optimizan su posición para maximizar la captación de energía solar, este dispositivo permite a los estudiantes observar cómo las células solares captan la luz y la transforman en corriente eléctrica, ilustrando de manera práctica el proceso del efecto fotovoltaico.

El demostrador incluye un panel solar ajustable, que ayuda a los estudiantes a explorar cómo la orientación del panel y el ángulo de incidencia de la luz solar afectan la eficiencia energética. Al igual que los girasoles siguen el sol a lo largo del día para maximizar su exposición, el demostrador destaca la importancia de la correcta alineación de los paneles solares para obtener un rendimiento óptimo.

Además de enseñar los principios técnicos de la energía fotovoltaica, el demostrador ofrece una experiencia educativa que conecta a los estudiantes con la naturaleza y fomenta una visión práctica y eficiente del aprovechamiento de recursos sostenibles.

10
- Demostrador de agua

El demostrador de agua es una herramienta educativa que permite a los estudiantes comprender cómo se puede capturar y gestionar el agua de lluvia de manera eficiente. A través de este dispositivo, los estudiantes observan el proceso de recolección de agua, desde la captación en una superficie similar a un tejado hasta su almacenamiento en un depósito. Esto les permite explorar el ciclo del agua y aplicar estrategias de conservación hídrica en la vida cotidiana.

El demostrador ilustra cómo el agua de lluvia, un recurso renovable y gratuito, puede ser aprovechada para diversas aplicaciones prácticas, como el riego de plantas. Además, los estudiantes aprenden sobre la importancia de mantener limpios los sistemas de captación y almacenamiento, así como sobre la relevancia de la sostenibilidad en el uso eficiente del agua, especialmente en zonas con escasez de recursos hídricos.

Inspirado en la estética y el funcionamiento del Bejeque, una suculenta autóctona de Canarias, este recolector de agua conecta la naturaleza y la tecnología moderna, demostrando cómo las soluciones basadas en la biomimética pueden preservar los recursos hídricos. Siguiendo la filosofía de integración artística y natural de César Manrique, el recolector fusiona arte, ecología y tecnología educativa, promoviendo el respeto por el medio ambiente y la cultura local, mientras enseña a los estudiantes a valorar y aplicar soluciones sostenibles inspiradas en la naturaleza para el futuro.

11

## 3. PROGRAMACIÓN DE LOS DEMOSTRADORES
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

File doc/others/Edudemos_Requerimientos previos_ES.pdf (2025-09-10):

# EDUcando a través de DEMOnstradores Sostenibles

# Requerimientos previos


Financiado por la Unión Europea. Las opiniones y puntos de vista expresados solo comprometen a su(s) autor(es) y no reflejan necesariamente los de la Unión Europea o los de la Agencia Ejecutiva Europea de Educación y Cultura (EACEA). Ni la Unión Europea ni la EACEA pueden ser considerados responsables de ellos.

EduDemoS 3in1 © 2025 by Gerda Stetter Stiftung – Technik macht Spaß! is licensed under Creative Commons Attribution-NonCommercial-ShareAlike 4.0 International. To view a copy of this license, visit https://creativecommons.org/licenses/by-nc-sa/4.0/

# Talleres EduDemoS

Durante el Taller EduDemoS desarrollaremos tres Demostradores Sostenibles diferentes:

### 1. Tortuga 2. Demostrador Modular 3x1 3. Rastreador Solar (Girasol)

Para saber más sobre estos demostradores y el Proyecto EduDemoS, visita el sitio web: https://edudemos.eu/

Cada demostrador cuenta con una guía que explica cómo construirlo. Para estar preparado para el Taller, puedes descargar y leer estas guías con antelación.
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

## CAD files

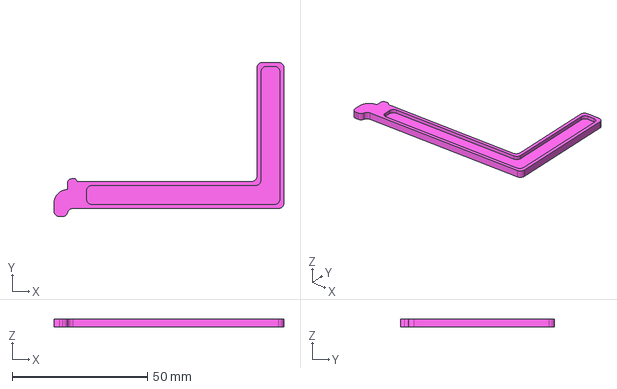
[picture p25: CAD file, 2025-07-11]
model/Aspa L pequeña_V3_x6.stp
85.0 x 57.0 x 3.00 mm

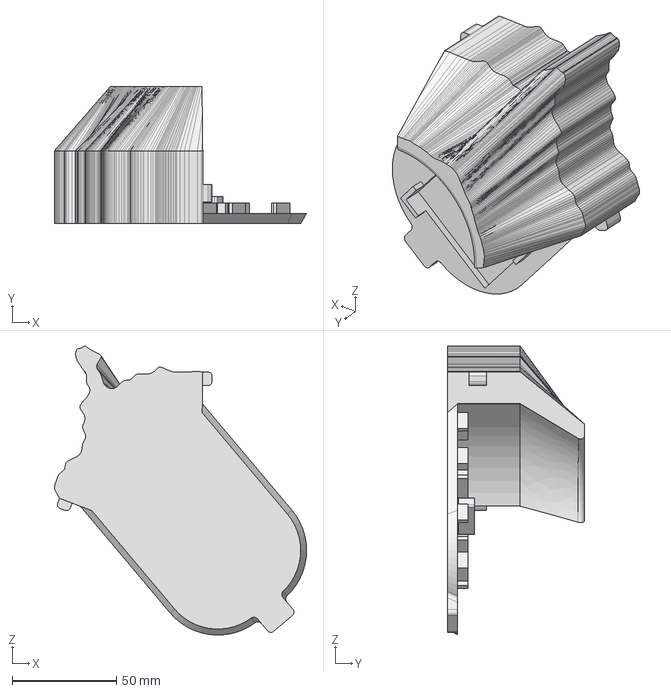
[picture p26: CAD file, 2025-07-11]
model/Cajón_V7_x1.stp
121.2 x 66.0 x 138.8 mm

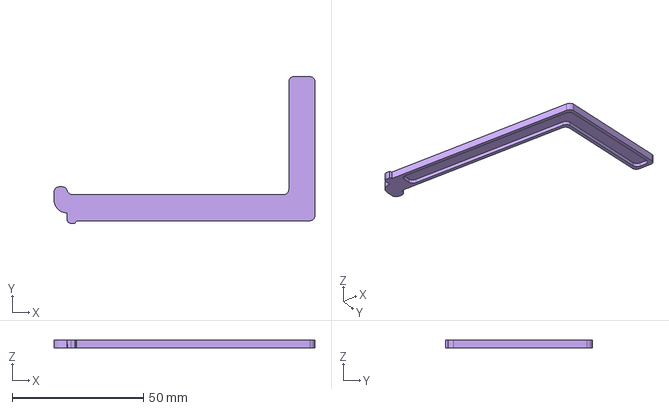
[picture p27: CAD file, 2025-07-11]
model/Aspa L grande_V3_x6.stp
99.5 x 56.0 x 3.00 mm

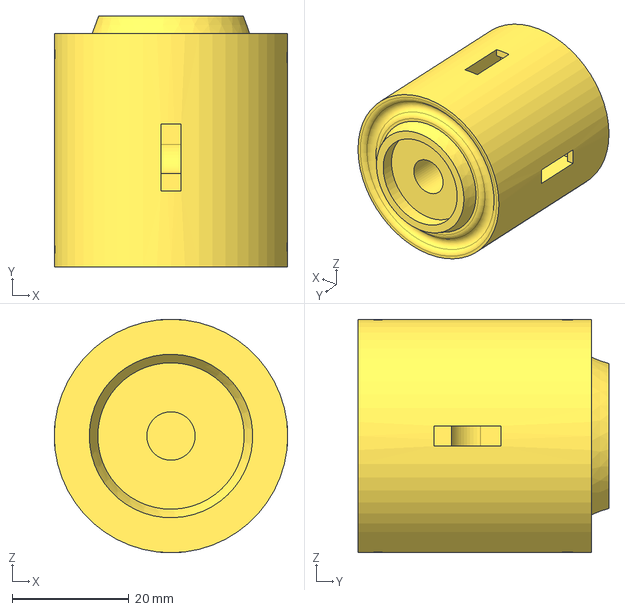
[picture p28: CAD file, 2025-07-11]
model/Disco grande_V5_x2.stp
40.0 x 43.0 x 40.0 mm

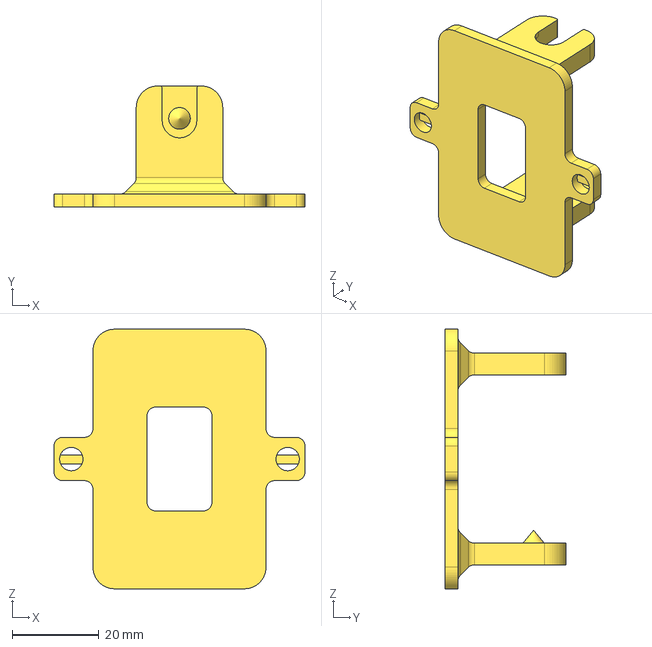
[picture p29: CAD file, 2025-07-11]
model/Placa sol_V5_x1.stp
58.0 x 28.0 x 60.0 mm

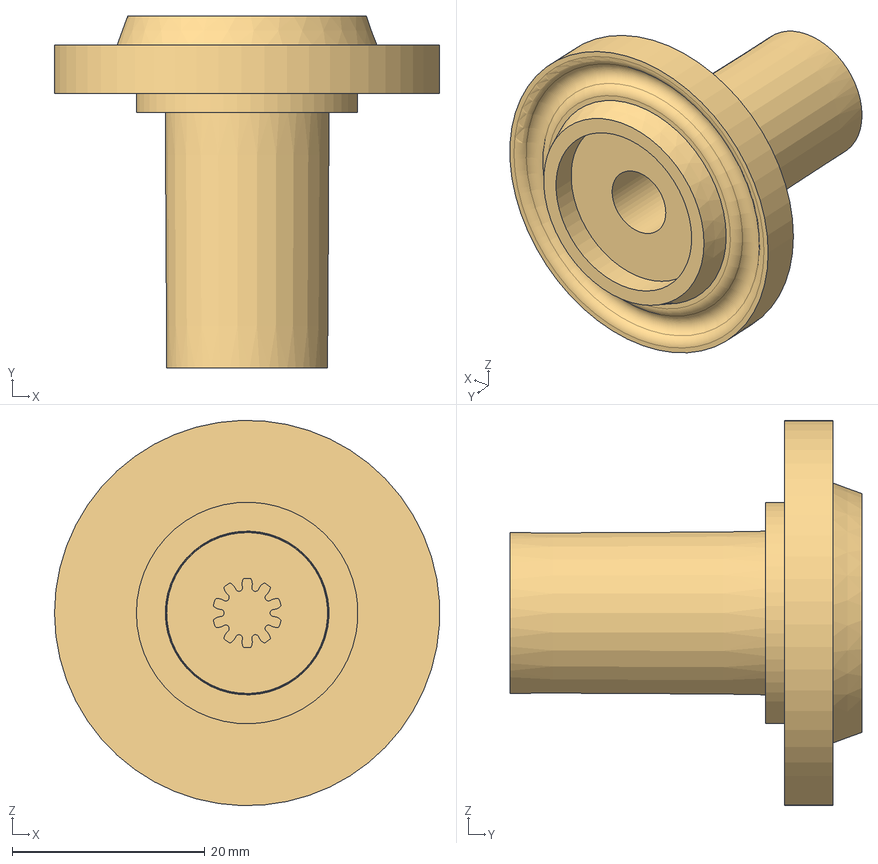
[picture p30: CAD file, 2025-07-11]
model/Disco rodamiento_V5_x1.stp
40.0 x 36.5 x 40.0 mm

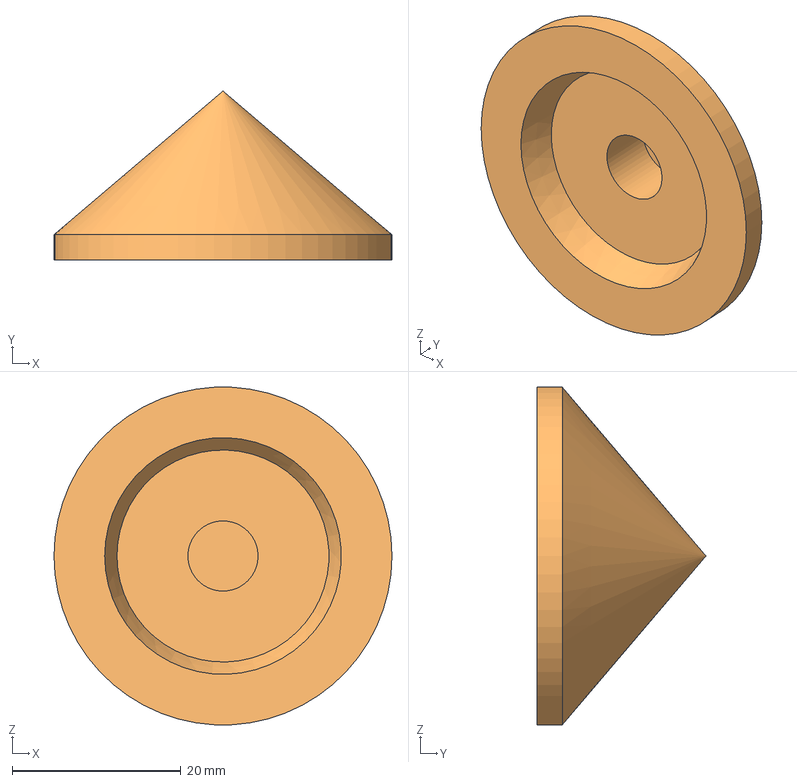
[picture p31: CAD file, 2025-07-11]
model/Tapa_V3_x1.stp
40.0 x 20.0 x 39.9 mm

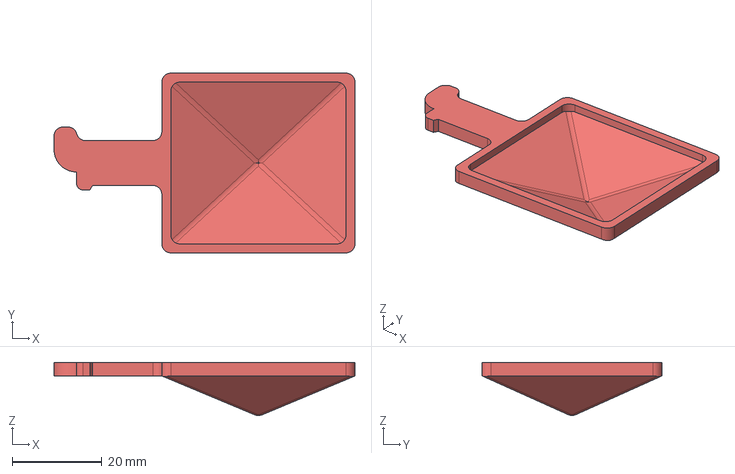
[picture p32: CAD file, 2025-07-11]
model/Aspa cuadrada_V4_x8.stp
67.0 x 40.0 x 11.8 mm

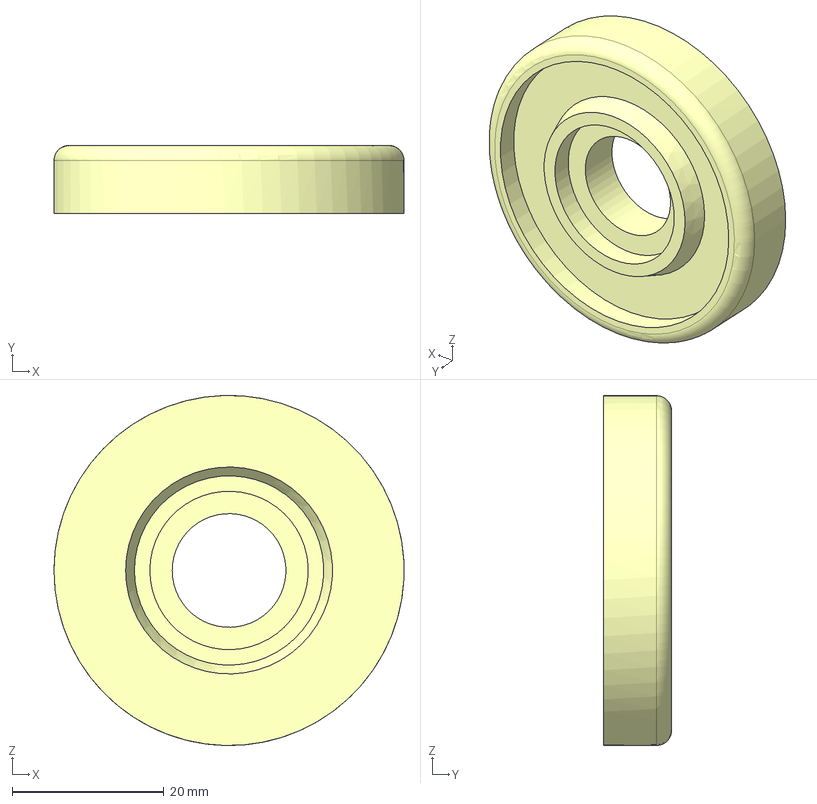
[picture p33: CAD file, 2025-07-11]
model/Disco estático_V7_x2.stp
46.2 x 9.00 x 46.2 mm

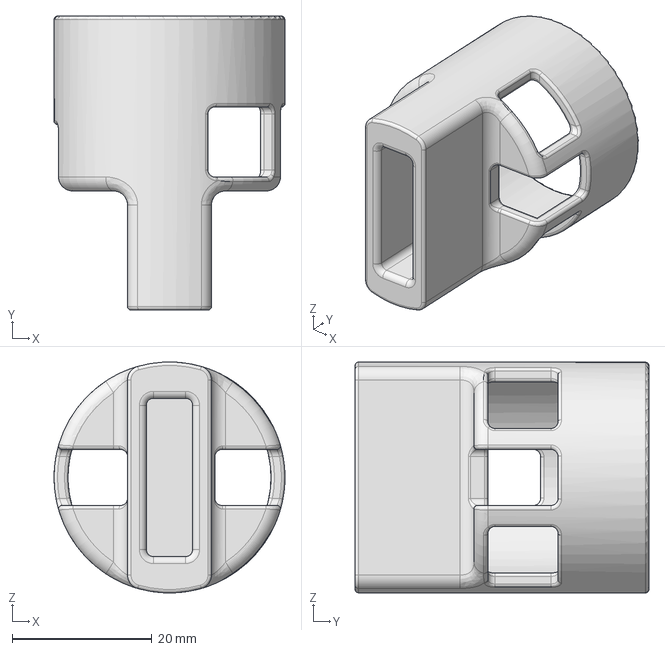
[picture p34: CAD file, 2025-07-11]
model/Encaje motor_V5_x1.stp
33.0 x 42.0 x 33.0 mm

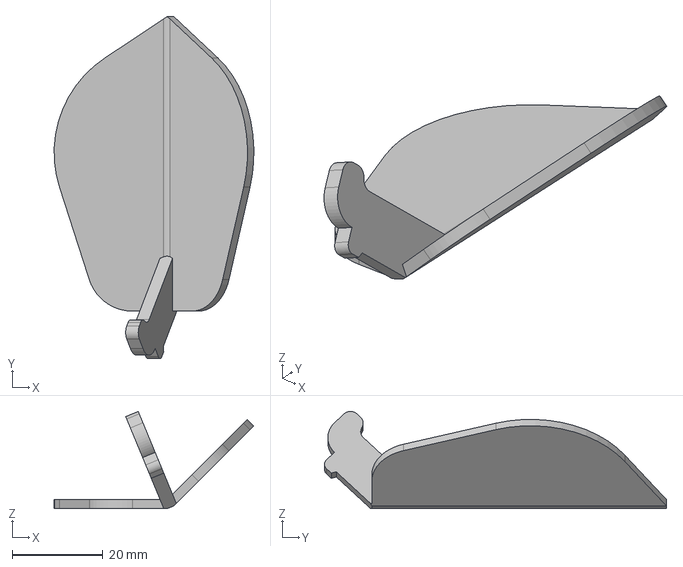
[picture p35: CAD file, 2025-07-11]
model/Hoja_V1_x8.stp
44.1 x 75.4 x 21.4 mm

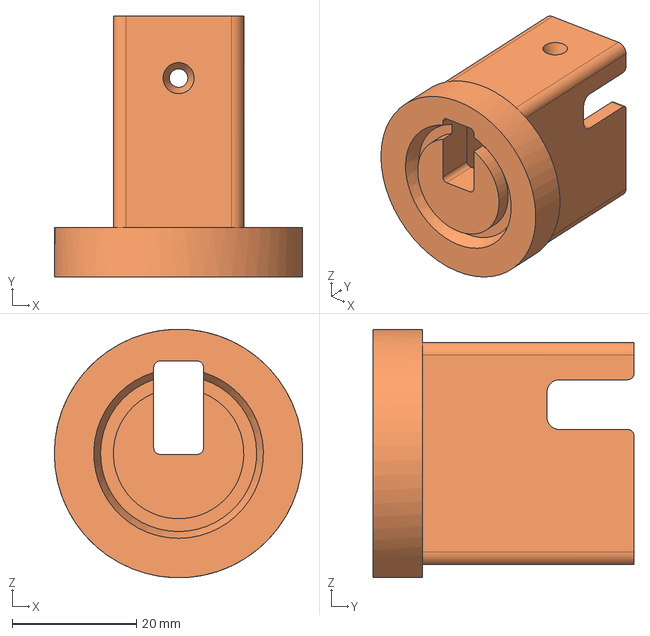
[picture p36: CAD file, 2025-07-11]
model/Disco sol_V6_x1.stp
40.0 x 42.0 x 40.0 mm

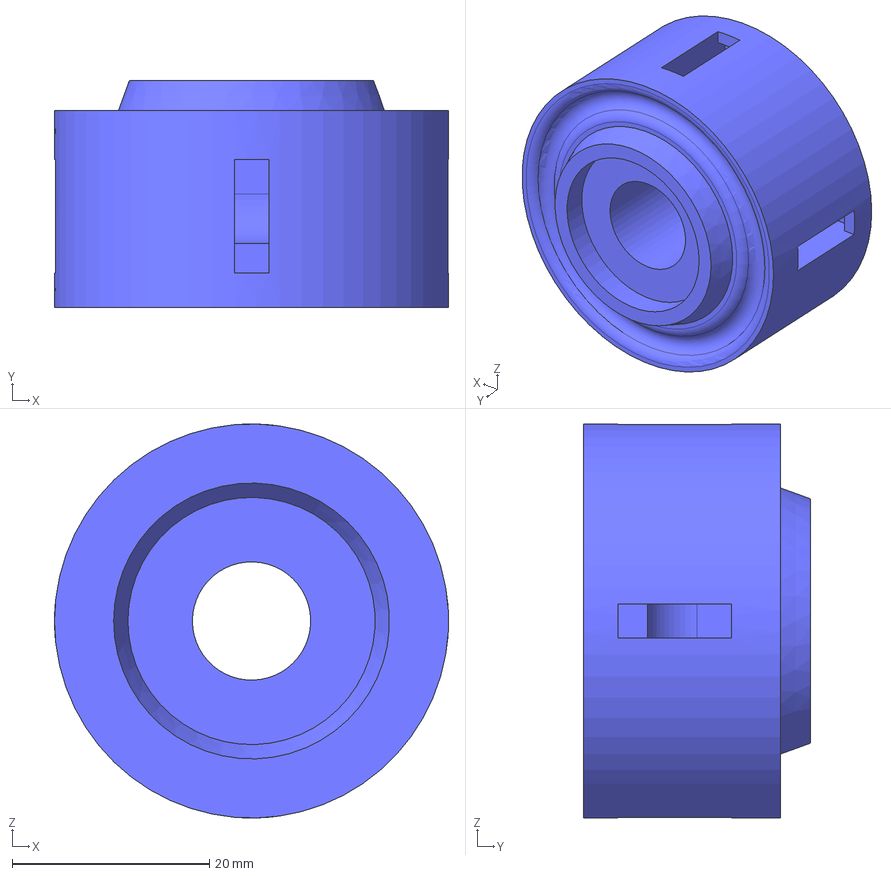
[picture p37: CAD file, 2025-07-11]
model/Disco pequeño_V5_x3.stp
40.0 x 23.0 x 40.0 mm

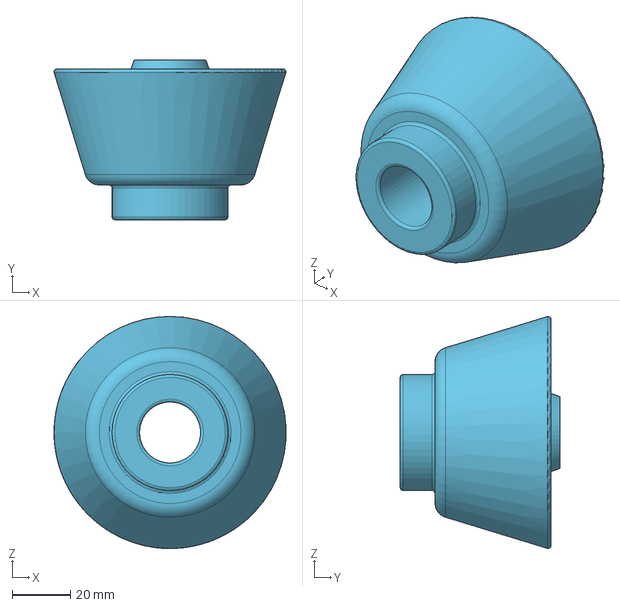
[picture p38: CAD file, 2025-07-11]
model/Contenedor agua_V7_x1.stp
80.0 x 55.0 x 80.0 mm

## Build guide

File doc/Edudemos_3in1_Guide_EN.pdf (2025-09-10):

## EDUDEMOS

Funded by the European Union. Views and opinions expressed are however those of the author(s) only and do not necessarily reflect those of the European Union or the European Education and Culture Executive Agency (EACEA). Neither the European Union nor EACEA can be held responsible for them.

EduDemoS 3in1 © 2025 by Gerda Stetter Stiftung – Technik macht Spaß!, Sergio Alonso Fundation, FINNOVA REGIO, GBS St. Gallen e IES El Rincón is licensed under
Creative Commons Attribution-NonCommercial-ShareAlike 4.0 International. To view a copy of this license, visit https://creativecommons.org/licenses/by-nc-sa/4.0/

1

Funded by the European Union. Views and opinions expressed are however those of the author(s) only and do not necessarily reflect those of the European Union or the European Education and Culture Executive Agency (EACEA). Neither the European Union nor EACEA can be held responsible for them.

1. INTRODUCTION TO EDUDEMOS | 4
1. 1. What is EduDemos? | 4
1. 2. Objectives | 4
1. 3. Methodology | 4
1. 4. Partners | 5
2. DEMONSTRATOR 3x1 | 6
2. 1. Description of the Models | 6
2. 1. 1. Objectives | 6
2. 1. 2. Educational Competencies | 7
2. 1. 3. Basic Concepts | 10
3. PROGRAMMING OF THE DEMONSTRATORS | 13
3. 1. Minimum Requirements | 13
3. 2. Required Libraries | 17
3. 3. Finding and Downloading the Code | 18
3. 4. How the Code Works | 20
3. 5. Programming the Microcontroller | 31
4. Introduction to Electronics | 32
4. 1. Ohm’s Laws | 32
4. 2. Electronic Components | 34
4. 2. 1. Basic Components | 34
4. 2. 2. Powering a Circuit | 38
4. 2. 3. Configuration of Components in a Circuit | 39
4. 2. 4. Sensors | 40
4. 2. 5. Actuators | 42
4. 3. Breadboard | 43
4. 3. 1. Activities with a Breadboard | 45
4. 3. 2. Voltage Divider | 47
4. 3. 3. Activities with Voltage Dividers | 48
5. ASSEMBLY OF THE 3-IN-1 DEMONSTRATOR | 49
5.1. List of Materials | 50

2
5. 2. Assembly of the Water and Solar Demonstrator | 51
5. 2. 1. Electronic Assembly (Water Component) | 51
5. 2. 2. Electronic Assembly (Solar Component) | 62
5. 2. 3. Mechanical Assembly of the Water and Solar Demonstrator | 75
5. 3. Assembly of the Wind Demonstrator | 82
5. 3. 1. Electronic Assembly | 82
5. 3. 2. Mechanical Assembly | 86
6. DATA FROM THE SENSORS | 94
6. 1. Serial Port | 94
6. 2. Adafruit IO | 97
7. OTA (Over-The-Air) UPDATES | 102
8. TYPICAL PROBLEMS | 103

3
This first section will contain all the necessary information to understand the project, its funding, objectives, and participants. The sections of this first block of the guide will be:

## 1. INTRODUCTION TO EDUDEMOS

### 1. 1. What is EduDemos?

EduDemos is an educational project that develops sustainable demonstrators based on renewable energies such as water, sun, and air. These demonstrators are interactive and replicable tools used to teach young people and teachers about sustainability and digital skills, integrating hands-on learning with environmental awareness.

### 1. 2. Objectives

The main objective of the EduDemos project is to raise awareness among new generations, both young people and teachers, about sustainability through the use of demonstrators based on renewable energies such as sun, water, and air. Additionally, it aims to enhance digital skills in the educational field by providing practical and replicable technological tools. Another of its purposes is to foster a collaborative network among educators to exchange knowledge and practical experiences, promoting the adoption of sustainable practices and contributing to a greener future in Europe.

### 1. 3. Methodology

The methodology of the EduDemos project is structured around the practical implementation of sustainable demonstrators that use renewable energy sources such as water, sun, and air. These demonstrators are not just theoretical tools; they are designed to be built and experienced by students, promoting active and hands-on learning.

4
- Model development: Demonstrator models integrating renewable energy technologies are designed. These models serve as practical examples that students can replicate.
- Construction guides: EduDemos provides detailed guides for the construction of these demonstrators, ensuring that students and teachers can follow the step-by-step process. These guides are accessible and designed to be used in an educational setting, facilitating the learning of technical and scientific concepts in a practical way.
- Teacher and student training: Training programs are implemented for both teachers and students. These programs are designed to develop skills in both sustainability and digital competencies, preparing participants to face the challenges of climate change. The training includes workshops, courses, and educational resources that complement theoretical learning with practical application.
- European collaboration: The project promotes collaboration between various educational institutions and organizations across Europe. This cooperative network enables the exchange of knowledge, experiences, and resources, enriching the educational process. The project partners work together to adapt and improve the models and guides according to local and regional needs, fostering more inclusive and effective education throughout Europe.

### 1. 4. Partners

The EduDemos project has several key partners who contribute their expertise and resources to the success of the project:

- Gerda Stetter Stiftung (Germany): This foundation specializes in educational and technological projects, with a focus on sustainable development. Its participation ensures that the technical and pedagogical aspects of the project are of high quality.

5
- Fundación Sergio Alonso (Spain): A foundation that supports educational and social initiatives, especially in the Canary Islands. Its contribution is crucial for the implementation of the project in Spain and for ensuring its local relevance.
- FINNOVAREGIO (Belgium): This organization focuses on regional innovation and sustainable development. Its role in EduDemos is key to integrating the project into European networks of innovation and sustainability.
- GBS St.Gallen (Switzerland): This Swiss educational institution brings its expertise in vocational and technical training, particularly in the field of renewable energies. It contributes to the development of the educational content and the project's methodology.
- IES El Rincón (Spain): A secondary education institute in Gran Canaria, Spain, that serves as one of the pilot centers where the project's sustainable demonstrators are implemented and tested. Its participation is essential for tailoring the project to the needs of students and teachers.

Each of these partners brings their specific expertise, enabling EduDemos to be a comprehensive project that addresses sustainability education from different perspectives and within various European contexts. The collaboration among these partners ensures that the resources developed are diverse, accessible, and applicable across different educational settings.

## 2. DEMONSTRATOR 3x1

### 2. 1. Description of the Models

2. 1. 1. Objectives

The objective of the demonstrators is to teach and raise awareness among students about how energy is generated from wind, sun, and water harvesting, promoting a practical understanding of renewable energies and the importance of

6
environmental sustainability. These demonstrators aim to engage students in the construction and experimentation with sustainable technologies, fostering technical skills and sustainability-related competencies.

These demonstrators are primarily designed for students in vocational education, but they can also be used at the secondary education level. Specifically, they target students from compulsory secondary education to high school and vocational training, where students already have a foundation in science and technology, enabling them to understand and experiment with more advanced concepts such as wind or solar energy.

Their educational value lies in their ability to provide a practical and contextualized learning experience around renewable energies. Through the construction and use of the 3-in-1 Demonstrator, students gain a deeper understanding of how energy is generated from wind, sun, and water harvesting, while also fostering technical skills, digital competencies, and a greater commitment to environmental sustainability. This facilitates active learning and the development of key competencies in science and technology.

2. 1. 2. Educational Competencies

The demonstrators support the development of key competencies in students pursuing vocational training, particularly those studying technical professional families, as well as students from 1st to 4th year of secondary education. Through their construction and analysis, students gain essential skills for their growth, while also fostering teamwork, applying creativity, and critical thinking to solve problems. Additionally, they will understand the impact of sustainable technologies on society. This approach promotes comprehensive training that prepares students to face current and future challenges.

Educational Competencies to Be Acquired with the 3-in-1 Demonstrator for 1st to 3rd Year ESO:

### 1. Linguistic Communication Competency (CCL):

7
Development of communication skills: Students will learn to communicate their ideas and results using appropriate technical language. This applies both to presenting technological solutions and preparing basic technical documentation.
2. Mathematical Competency and STEM (Science, Technology, Engineering, and Mathematics):
Application of scientific and technological knowledge: Students will apply basic physics and technology concepts to understand and explain the functioning of the 3-in-1 Demonstrator, including the interpretation and design of simple electrical circuits and diagrams.

### 3. Digital Competency (CD):

Use of digital tools: The use of software for project design and simulation will be fundamental. Students will learn to use digital applications to represent diagrams, circuits, and design components of the 3-in-1 Demonstrator.

### 4. Personal, Social, and Learning to Learn Competency (CPSAA):

Teamwork and self-regulation: Through collaboration in constructing and evaluating the Demonstrator, students will develop teamwork skills, self-regulation, and critical reflection on their learning process.

### 5. Entrepreneurial Competency (CE):

Creativity and problem-solving: Students will be challenged to come up with creative and sustainable solutions to improve the performance of the 3-in-1 Demonstrator, fostering an entrepreneurial mindset that values innovation and sustainability.

### 6. Cultural Awareness and Expression Competency (CCEC):

Cultural and technological appreciation: Students will reflect on the importance of sustainable technologies in different cultural contexts, recognizing the value of technological heritage and its impact on society.

These competencies are acquired through a practical and contextualized approach around the 3-in-1 Demonstrator, allowing students to develop essential skills that are relevant both in their academic and personal lives.

8

Educational Competencies to Be Acquired with the 3-in-1 Demonstrator for 4th Year ESO:

### 1. Linguistic Communication Competency (CCL):

Participation in collaborative projects: Students will develop the ability to effectively communicate their ideas and results in various formats (oral, written, visual) using appropriate and respectful technical language. The use of inclusive and non-sexist language in all project-related communication will also be promoted.

2. Mathematical Competency and STEM (Science, Technology, Engineering, and Mathematics):
Design and manufacture of solutions: Students will apply knowledge of mathematics, science, and technology to design and build the Demonstrator, using computer-aided design (CAD) tools and digital manufacturing techniques (such as 3D printing). Additionally, they will analyze the product life cycle to ensure that solutions are sustainable and efficient.

### 3. Digital Competency (CD):

Use of digital tools: Students will use digital applications and platforms to manage the project from ideation to final presentation. They will learn to validate and cross-check information using reliable digital sources, and configure digital tools as needed to optimize their learning and solve technological problems.

### 4. Personal, Social, and Learning to Learn Competency (CPSAA):

Teamwork and project management: Throughout the project, students will be encouraged to work effectively as a team, sharing responsibilities and

9
collaborating to solve problems. Self-reflection and continuous improvement of the learning process will also be promoted through critical evaluation of proposed solutions.

### 5. Entrepreneurial Competency (CE):

Creativity and innovation: Students will be encouraged to develop innovative technological solutions that create value for the community, using problem-solving strategies and fostering an entrepreneurial spirit. The planning and execution of sustainable and accessible projects will be key in this process.

### 6. Cultural Awareness and Expression Competency (CCEC):

Expression and dissemination of ideas: Students will learn to express and disseminate their technological proposals creatively and effectively, using various media and techniques. The importance of valuing artistic and cultural creation in technology will be emphasized, promoting an ethical and socially responsible approach to their projects.

These competencies are designed to ensure that students not only acquire technical knowledge but also develop transversal skills and a critical, sustainable mindset, essential in the context of secondary education.

2. 1. 3. Basic Concepts
- Wind demonstrator

The wind demonstrator is an educational tool that allows students to build a small wind turbine to understand the basic principles of wind energy and its application in generating electricity. Through interaction with the device, students learn how the kinetic energy of the wind is first transformed into mechanical energy by the movement of the blades, and then into electrical energy thanks to a generator.

This demonstrator includes essential components such as blades, a shaft, and a generator, facilitating practical understanding of concepts like blade aerodynamics,

10
the relationship between wind speed and energy efficiency, and the environmental impact of wind energy compared to other energy sources. It also allows students to explore how the design and orientation of the blades influence the maximization of energy generation.

Inspired by César Manrique's "Wind Toys," this device merges art and educational functionality, connecting the cultural heritage of the Canary Islands with the teaching of renewable energy. It is a tool that not only promotes technical learning but also celebrates the harmony between nature, technology, and local culture.

- Solar demonstrator

The solar demonstrator is an educational tool designed to help students understand how sunlight is converted into electricity through photovoltaic panels. Inspired by the movement of sunflowers, which optimize their position to maximize solar energy capture, this device allows students to observe how solar cells capture light and transform it into electrical current, practically illustrating the photovoltaic effect.

The demonstrator includes an adjustable solar panel, enabling students to explore how the panel's orientation and the angle of sunlight impact energy efficiency. Just as sunflowers follow the sun throughout the day to maximize exposure, the demonstrator emphasizes the importance of proper alignment of solar panels for optimal performance.

In addition to teaching the technical principles of photovoltaic energy, the demonstrator provides an educational experience that connects students with nature and fosters a practical and efficient perspective on harnessing sustainable resources.

- Water demonstrator

The water demonstrator is an educational tool that allows students to understand how rainwater can be efficiently captured and managed. Through this device, students observe the water collection process, from the capture on a roof-like surface to its storage in a reservoir. This helps them explore the water cycle and apply water conservation strategies in everyday life.

11

The demonstrator illustrates how rainwater, a renewable and free resource, can be utilized for various practical applications, such as plant irrigation. Additionally, students learn about the importance of keeping collection and storage systems clean, as well as the significance of sustainability in efficient water use, especially in areas with limited water resources.

Inspired by the aesthetics and functionality of the Bejeque, a native succulent of the Canary Islands, this water collector connects nature with modern technology, demonstrating how biomimetic solutions can help preserve water resources. Following the philosophy of artistic and natural integration promoted by César Manrique, the collector merges art, ecology, and educational technology, encouraging respect for the environment and local culture, while teaching students to value and apply nature-inspired sustainable solutions for the future.

12

## 3. PROGRAMMING OF THE DEMONSTRATORS

### 3. 1. Minimum Requirements

The demonstrators use a programmable board called ESP32. To begin programming this board from a PC, several key aspects must be considered.

First, we need to have the IDE (Integrated Development Environment) installed, which serves as the interface that allows us to program our board. The ESP32 is compatible with the Arduino IDE, which is well-known and easy to use. To download the application, we need to visit the official Arduino website. (https://www.arduino.cc/en/software) For PC users, the easiest option is to select the appropriate version based on the operating system of the computer. This will download an executable file that will install the development tool.

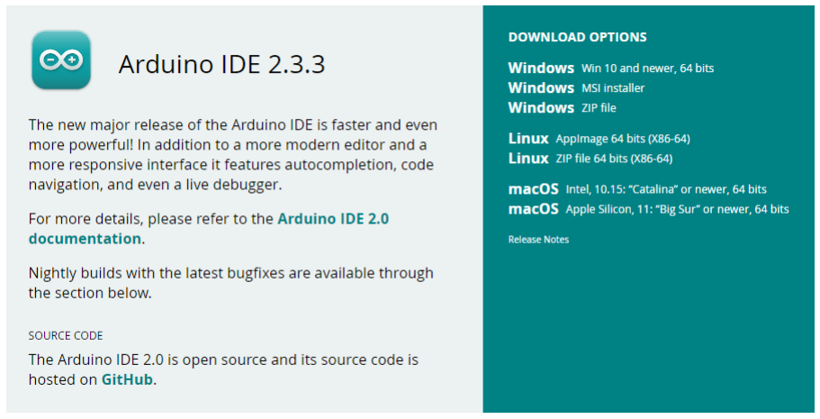
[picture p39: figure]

13
Note: in the Edudemos website (https://edudemos.eu/en/demonstrators/) > demonstrators > 3x1 demonstrator > guide you will find the document “Previous Requirements”, where it explains step by step how to install the Arduino software, the drivers, libraries, and the main code.

14
Secondly, the application communicates with the board through one of the computer's USB ports, using a serial communication protocol. To facilitate this communication, the board has a small integrated chip dedicated to this function. On the ESP32 board with ESP32, this function is performed by the CP2102 chip. If the computer does not automatically detect the board when connected via USB, we will need to install the appropriate drivers. These drivers can be downloaded from the manufacturer's website. (https://www.silabs.com/developers/usb-to-uart-bridge-vcp-drivers?tab=downloads)

Thirdly, before being able to program the ESP32, you need to add support for the ESP32 board in the Arduino IDE. To do this, go to Tools > Board > Board Manager and search for "ESP32." Install the support package created by the microcontroller's manufacturer, "Espressif Systems," for that board. You should now have a list of boards available, including the "ESP32-WROOM-DA", which we will use throughout this guide.

15

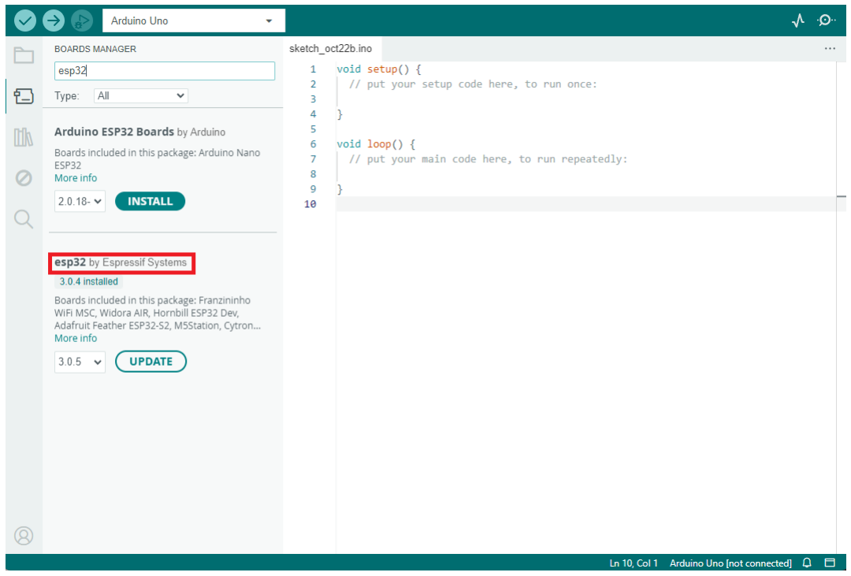
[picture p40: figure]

Lastly, you only need to select the port where the board is connected to the computer via a micro USB to USB Type-A cable. Serial ports are selected at the top of the Arduino IDE under the Tools > Port tab. From there, choose the port where the board is connected.

16

If you're unsure which port is assigned to the ESP32, you can disconnect and reconnect the board to identify it. On Windows, the port will appear as COMX (where X is the port number). On other operating systems, like macOS or Linux, the ports may be displayed as /dev/ttyUSBX or /dev/ttySX. By disconnecting and reconnecting the board, observe which port appears or disappears from the list to identify the correct one.

17

### 3. 2. Required Libraries

An Arduino IDE library is a set of pre-written code that simplifies programming by providing ready-to-use functions and procedures. These libraries group together commands and tools that allow interaction with specific components and modules, such as sensors, motors, displays, and more, without the need to write all the code from scratch. By including a library in your project, you can simplify complex tasks and make your code cleaner and easier to understand.

At this stage, you'll need to install several libraries that are necessary for the microcontroller code (we'll explain how to download it in the next section) to function correctly. These libraries will allow proper sensor readings and facilitate the connection of the Demonstrators to the internet.

18
Within the Arduino IDE, go to the Tools > Manage Libraries tab, search for the necessary libraries for the code: ArduinoJson, Adafruit_WiFi, and DHT sensor library, and install them.

### 3. 3. Finding and Downloading the Code

The code for the Demonstrators can be found in the official EDUDEMOS repository on GitHub, an online platform that allows developers to store, manage, and collaborate on programming projects. User repositories serve to host their code, collaborate with other developers, and manage software versions.
Visit the official GitHub page and search for the EDUDEMOS repository. (https://github.com/Gadeschii/EDUDEMOS) You should see a page like the following:

19

You can find the source code for the Demonstrators in the src/main/ folder in the main_2.ino file. Within GitHub, you can open it to view the program. There are two ways to obtain the code: by downloading the file using the download button or by copying the lines of code and pasting them into an empty file in your Arduino IDE using the copy button.

20
In the repository, you will find a file called README.md, which explains the code and the functions it uses. You can refer to it whenever you need.

### 3. 4. How the Code Works

The source code implemented for an ESP32 microcontroller in this case allows for the measurement of temperature and humidity, LED control based on temperature values, the use of an LDR to control a servo motor, and the measurement of a generated direct current voltage. Below, the code is broken down and explained in parts to provide an overview of its functionality.

In the setup() function, serial communications are initialized, the WiFi connection is configured, OTA (Over The Air) updates are enabled, and both the DHT sensor and the LEDs and servo motor are prepared for use. Additionally, FreeRTOS tasks are created to manage data readings from the sensor and the voltage generated by the motor.

void setup() {

Serial.begin(115200); // Start serial communication at 115200 baud rate

analogReadResolution(12); // ESP32 has a 12-bit ADC

analogSetAttenuation(ADC_11db); // Set attenuation for higher sensitivity

pinMode(4, INPUT);

setupWiFi(); // Setup WiFi connection

setupOTA(); // Setup OTA for remote updates

setupDHT(); // Setup DHT sensor

setupLEDsAndServo(); // Setup LED pins and servo

// Create tasks

xTaskCreatePinnedToCore(

readSensorTask1, // Task function

"ReadSensorTask1", // Name of the task

4096, | // Stack size
NULL, | // Task input parameter
1, | // Priority of the task
NULL, | // Task handle
0 | // Core where the task should run

21

);

xTaskCreatePinnedToCore(

readSensorTask2, // Task function

"ReadSensorTask2", // Name of the task

4096, | // Stack size
NULL, | // Task input parameter
1, | // Priority of the task
NULL, | // Task handle
1 | // Core where the task should run

);

xTaskCreatePinnedToCore(

readDcMotorVoltageTask, // Task function

"readDcMotorVoltageTask", // Name of the task

4096, | // Stack size
NULL, | // Task input parameter
1, | // Priority of the task
NULL, | // Task handle
1 | // Core where the task should run

);

xTaskCreatePinnedToCore(

readSolarVoltageTask, // Task function

"readSolarVoltageTask", // Name of the task

4096, | // Stack size
NULL, | // Task input parameter
1, | // Priority of the task
NULL, | // Task handle
1 | // Core where the task should run

);

}

The main program cycle, the loop() function, is responsible for handling OTA updates and maintaining a continuous connection to Adafruit IO.

void loop() {

handleOTA(); // Handle OTA updates

io.run(); // Maintain connection to Adafruit IO

}

22
The readDcMotorVoltage() function is responsible for reading the voltage generated by a direct current motor through a voltage sensor, converting this measurement into microvolts. The data is sent to Adafruit IO after performing multiple readings to reduce error, and a minimum threshold is applied to filter out unwanted noise. Similarly, the readSolarVoltage() function is designed to measure the output from a voltage detector connected to a solar panel. As with the previous function, multiple readings are taken to minimize noise and improve data accuracy.

void readDcMotorVoltage() {

// Take multiple readings to reduce noise

const int numReadings = 1000;

unsigned long sum = 0;

for (int i = 0; i < numReadings; i++) {

int reading = analogRead(DcMotorPin);

sum += reading;

}

float averageReading = sum / (float)numReadings;

Serial.print("Average ADC reading: ");

Serial.println(averageReading); // Display the average value

// Calculate voltage

float voltage = (averageReading / 4095.0) * 3.3; // For 12-bit ADC (0-4095)

Serial.print("Measured voltage (V): ");

Serial.println(voltage); // Display the measured voltage

// Adjust for voltage divider

float inputVoltage = voltage / (R2 / (R1 + R2));

// Convert to microvolts

float microvoltsMotorDc = inputVoltage * 1000000.0;

Serial.print("Input voltage (µV): ");

Serial.println(microvoltsMotorDc);

// Apply a minimum threshold to filter noise

const float threshold = 10.0; // Threshold in microvolts

if (microvoltsMotorDc < threshold) {

microvoltsMotorDc = 0;

}

// Check if the microvolts value has changed

23

if (microvoltsMotorDc != lastMicrovolts) {

Serial.print("Measured voltage: ");

Serial.print(microvoltsMotorDc, 2); // Display with 2 decimal places

Serial.println(" µV");

// Send microvolts to Adafruit IO

microvoltsMotorDcFeed->save(microvoltsMotorDc);

// Update the last microvolts value

lastMicrovolts = microvoltsMotorDc;

}

}

void readSolarVoltage() {

// Take multiple readings to reduce noise

const int numReadings = 1000;

unsigned long sum = 0;

for (int i = 0; i < numReadings; i++) {

int reading = analogRead(SolarPin);

sum += reading;

}

float averageReading = sum / (float)numReadings;

Serial.print("Average ADC reading: ");

Serial.println(averageReading); // Display the average value

// Calculate voltage

float voltage = (averageReading / 4095.0) * 3.3; // For 12-bit ADC (0-4095)

Serial.print("Measured voltage (V): ");

Serial.println(voltage); // Display the measured voltage

// Adjust for voltage divider

float inputVoltage = voltage / (R2 / (R1 + R2));

// Convert to microvolts

float microvoltsSolar = inputVoltage * 1000000.0;

Serial.print("Input voltage (µV): ");

Serial.println(microvoltsSolar);

// Apply a minimum threshold to filter noise

const float threshold = 10.0; // Threshold in microvolts

if (microvoltsSolar < threshold) {

microvoltsSolar = 0;

24

}

// Check if the microvolts value has changed

if (microvoltsSolar != lastMicrovolts) {

Serial.print("Measured voltage: ");

Serial.print(microvoltsSolar, 2); // Display with 2 decimal places

Serial.println(" µV");

// Send microvolts to Adafruit IO

microvoltsSolarFeed->save(microvoltsSolar);

// Update the last microvolts value

lastMicrovolts = microvoltsSolar;

}

}

The program utilizes several FreeRTOS tasks. The readSensorTask1() task is executed periodically to read and process temperature and humidity data from the DHT sensor. These data are sent to Adafruit IO, and based on the measured temperature, the LEDs are controlled accordingly. Meanwhile, the readSensorTask2() task reads values from two LDRs (light-dependent resistors), calculates the light difference between them, and adjusts the servo motor accordingly. It also sends the average LDR values to Adafruit IO. Another task, readDcMotorVoltageTask(), is dedicated to periodically reading and processing the motor voltage and sending this data to Adafruit IO. Finally, readSolarVoltageTask() measures the voltage from the detector and updates it on the platform along with the rest of the information.

void readSensorTask1(void * parameter) {

for (;;) {

Serial.println("----------------------- Measured Temperature / Humidity -------

---------------- ");

updateSensorData(); // Read and process sensor data

vTaskDelay(SENSOR_INTERVAL_5_MIN / portTICK_PERIOD_MS); // Delay for 5 minutes

}

}

void readSensorTask2(void * parameter) {

for (;;) {

Serial.println("----------------------------- Measured LDR and Servo ----------

------------------- ");

updateLDRAndServo(); // Read LDR values and control servo

25

vTaskDelay(SENSOR_INTERVAL_10_SEC / portTICK_PERIOD_MS); // Delay for 10

seconds

}

}

void readSolarVoltageTask(void * parameter) {

for (;;) {

Serial.println("----------------------------- Measured Solar (V) --------------

-------------- ");

readSolarVoltage(); // Read and process voltage

vTaskDelay(SENSOR_INTERVAL_10_SEC / portTICK_PERIOD_MS); // Delay for 10

seconds

}

}

void readDcMotorVoltageTask(void * parameter) {

for (;;) {

Serial.println("----------------------------- Measured DC Motor (V) -----------

----------------- ");

readDcMotorVoltage(); // Read and process voltage

vTaskDelay(SENSOR_INTERVAL_5_MIN / portTICK_PERIOD_MS); // Delay for 10 seconds

}

}

Regarding connectivity, the setupWiFi() function connects the ESP32 to a WiFi network and maintains the connection with Adafruit IO. For remote updates, the setupOTA() function initializes the OTA update system using the ArduinoOTA library, defining the handlers to manage these events. The handleOTA() function is responsible for managing OTA updates by invoking ArduinoOTA.handle().

void setupWiFi() {

int retries = 0;

const int maxRetries = 5;

WiFi.begin(WIFI_SSID, WIFI_PASS);

Serial.print("Connecting to WiFi");

while (WiFi.status() != WL_CONNECTED && retries < maxRetries) {

delay(1000);

Serial.print(".");

retries++;

}

26

if (WiFi.status() == WL_CONNECTED) {

Serial.println("\nConnected to WiFi");

// Send microvolts to Adafruit IO

wifiFeed->save(WIFI_SSID);

} else {

Serial.println("\nWiFi connection failed. Restarting...");

ESP.restart();

}

connectToAdafruitIO();

}

void handleOTA() {

ArduinoOTA.handle(); // Handle OTA updates

//check if there are new client

// Verificar si hay un nuevo cliente telnet

if (telnetServer.hasClient()) {

if (!telnetClient || !telnetClient.connected()) {

if (telnetClient) telnetClient.stop();

telnetClient = telnetServer.available();

Serial.println("New Telnet client connected");

} else {

telnetServer.available().stop();

}

}

//Send data to the telnet client server

if (telnetClient && telnetClient.connected()) {

while (Serial.available()) {

telnetClient.write(Serial.read());

}

while (telnetClient.available()) {

Serial.write(telnetClient.read());

}

}

}

void setupOTA() {

// Start telnet server

telnetServer.begin();

telnetServer.setNoDelay(true);

27

// Initialize ArduinoOTA for over-the-air updates

ArduinoOTA.setHostname("ESP32-OTA");

ArduinoOTA.setPassword("admin"); // Uncomment to set a password for OTA updates

// Define OTA event handlers

ArduinoOTA.onStart([]() {

String type;

if (ArduinoOTA.getCommand() == U_FLASH) {

type = "sketch";

} else { // U_SPIFFS

type = "filesystem";

}

Serial.println("Start updating " + type);

});

ArduinoOTA.onEnd([]() {

Serial.println("\nOTA Update Finished");

});

ArduinoOTA.onProgress([](unsigned int progress, unsigned int total) {

Serial.printf("Progress: %u%%\r", (progress / (total / 100)));

});

ArduinoOTA.onError([](ota_error_t error) {

Serial.printf("Error[%u]: ", error);

if (error == OTA_AUTH_ERROR) {

Serial.println("Auth Failed");

} else if (error == OTA_BEGIN_ERROR) {

Serial.println("Begin Failed");

} else if (error == OTA_CONNECT_ERROR) {

Serial.println("Connect Failed");

} else if (error == OTA_RECEIVE_ERROR) {

Serial.println("Receive Failed");

} else if (error == OTA_END_ERROR) {

Serial.println("End Failed");

}

});

ArduinoOTA.begin(); // Start the OTA service

Serial.println("OTA Ready");

}
Within the code itself, there are constant variables defined that contain the credentials for the Wi-Fi network to be used and the corresponding keys for the Adafruit IO platform. You can modify the values of these variables from line 30 onward, as shown below, if needed.

// Set up your wifi Credencial

28

#define WIFI_SSID "wifi_name"

#define WIFI_PASS "Wifi_Password"

// Set up your API key for Adafruit IO

#define AIO_USERNAME "Adafuit_name"

#define AIO_KEY "Adafruit_Password"

The DHT sensor is initialized in the setupDHT() function, and the pins for the LEDs and the servo motor are configured in the setupLEDsAndServo() function, which also connects the motor to its corresponding pin.

void setupDHT() {

dht.begin(); // Start the DHT sensor

}

Finally, there are two key functions for data updates: updateSensorData() reads the temperature and humidity values from the DHT sensor, sends this information to Adafruit IO, and controls the LEDs based on the temperature. The updateLDRAndServo() function reads the values from two LDRs, adjusts the servo motor according to the difference in light, and sends the average LDR values to Adafruit IO.

void updateSensorData() {

// Read values from DHT sensor

float h = dht.readHumidity();

float t = dht.readTemperature();

// Check if readings are valid

if (isnan(h) || isnan(t)) {

Serial.println("Failed to read from DHT sensor!");

return;

}

// Send values to Adafruit IO

temperature->save(t);

humidity->save(h);

// Print sensor values

Serial.print("Temperature: ");

Serial.print(t);

Serial.print(" °C, Humidity: ");

29

Serial.print(h);

Serial.println(" %");

// Example LED control based on temperature

if (t < 20) {

digitalWrite(ledPin1Cold, HIGH);

digitalWrite(ledPin2Good, LOW);

digitalWrite(ledPin3Heat, LOW);

// Send to the corresponding feed (Cold LED)

ledColdFeed->save(1); | // 1 means the LED is ON
ledGoodFeed->save(0); | // OFF
ledHighFeed->save(0); | // OFF

Serial.println("Cold is HIGH");

} else if (t >= 20 && t < 25) {

digitalWrite(ledPin1Cold, LOW);

digitalWrite(ledPin2Good, HIGH);

digitalWrite(ledPin3Heat, LOW);

// Send to the corresponding feed (Good LED)

ledColdFeed->save(0); | // OFF
ledGoodFeed->save(1); | // ON
ledHighFeed->save(0); | // OFF

Serial.println("Good is HIGH");

} else {

digitalWrite(ledPin1Cold, LOW);

digitalWrite(ledPin2Good, LOW);

digitalWrite(ledPin3Heat, HIGH);

// Send to the corresponding feed (Heat LED)

ledColdFeed->save(0); | // OFF
ledGoodFeed->save(0); | // OFF
ledHighFeed->save(1); | // ON

Serial.println("Heat is HIGH");

}

}

void updateLDRAndServo() {

// Read LDR values

ldrValue1 = analogRead(ldrPin1) ;

ldrValue2 = analogRead(ldrPin2)- OFFSET;

// Invert readings so low values mean darkness and high values mean light

ldrValue1 = 4095 - ldrValue1;

ldrValue2 = 4095 - ldrValue2;

averageLdrValue = (ldrValue1 + ldrValue2) / 2;

30

// Print readings for debugging

Serial.print("LDR 1: ");

Serial.print(ldrValue1);

Serial.print(" | LDR 2: ");

Serial.println(ldrValue2);

Serial.print("Average LDR: ");

Serial.println(averageLdrValue);

// Send the average value to Adafruit IO

ldrFeed->save(averageLdrValue);

ldr1Feed-> save (ldrValue1);

ldr2Feed -> save (ldrValue2);

// Compare LDR values and move the servo based on the difference

if (ldrValue1 > ldrValue2 + tolerance) {

if (servoPos > 0) {

servoPos -= servoStep; // Move the servo to the left

Serial.println("Moving left");

}

} else if (ldrValue2 > ldrValue1 + tolerance) {

if (servoPos < 180) {

servoPos += servoStep; // Move the servo to the right

Serial.println("Moving right");

}

}

// Ensure the servo stays within the [0, 180] range

servoPos = constrain(servoPos, 0, 180);

// Move the servo to the new position only if it has changed

myServo.write(servoPos);

// Print the servo angle

Serial.print("Servo angle: ");

Serial.println(servoPos);

// Pause to give the servo time to move

delay(30); // Increase the delay for more response time for the servo

}

31

### 3. 5. Programming the Microcontroller

To program the ESP32 board with the provided code, the first step is to have the ESP32 connected to the computer using a Micro USB to USB Type-A cable. Then, as previously mentioned, you will select the corresponding COM port for your board and use the Upload button in the Arduino IDE, which compiles the program before sending it to the programmable board. Just to the left of this button, with the tick symbol, is the Verify button, which only compiles the code. Compilation converts the written code, in a programming language like C/C++, into a format the microcontroller can understand and execute, while checking for syntax errors or issues that could prevent the program from running properly during the process.

If you encounter any errors related to the uploading process or loading the code onto the board, you can check the following:

- Check that the USB cable is properly connected at both ends.
- Try using a different USB cable, as some cables are only for charging and do not transmit data.
- Try using a different USB port on your computer.
- Ensure that you have selected the correct COM port.
- Some ESP32 models require manual programming mode activation by pressing the BOOT button as the code upload process begins.
- Verify that the necessary driver for programming the ESP32 (CP210x) is correctly installed.

32

## 4. Introduction to Electronics

Electronics is a branch of physics and engineering that focuses on the study, design, and application of devices and systems that operate by controlling electrons and other electrically charged particles. Through electronics, circuits are built that enable signal manipulation, facilitating the creation of essential technologies such as computers, phones, cars, and a wide variety of everyday devices.

### 4. 1. Ohm’s Laws

In the field of electronics and electricity, there is a key law known as Ohm's Law, which defines the relationship between the three most important quantities in a circuit: voltage (tension), current (intensity), and resistance. Understanding the meaning of these quantities and how they relate to each other may seem complex at first, but it becomes much easier when comparing an electrical circuit to a water system, using an analogy to explain its operation.

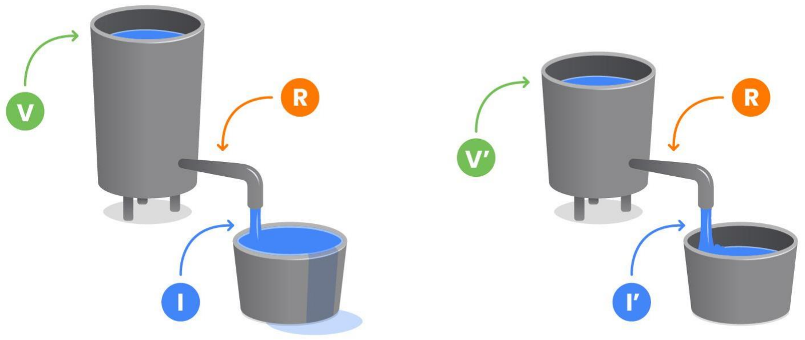
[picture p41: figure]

33
- Voltage (Tension): It is the water pressure in the pipes. Voltage is what "pushes" electrons (the current) to move through the circuit. It is measured in volts (V).
- Current (Intensity): It is the flow of water through the pipes. In an electrical circuit, it is the flow of electrons driven by the voltage. It is measured in amperes (A).
- Resistance: It is the size or narrowing of the pipe. Resistance is what "hinders" or "slows down" the flow of current. If the resistance is high, less current can pass through. It is measured in ohms (Ω).

Ohm's Law states that the relationship between these three quantities follows a simple rule:

Or in other forms:

- If you increase the voltage (the pressure), more current will flow.
- If you increase the resistance (narrow the pipe), less current will pass, unless you also increase the voltage.

34

### 4. 2. Electronic Components

Electronic components are the basic building blocks that make up electrical and electronic circuits. Each one performs a specific function within the circuit, allowing control and manipulation of the flow of electric current. Among the most common components are resistors, which limit current flow; capacitors, which store and release energy; diodes, which allow current to flow in only one direction; and transistors, which act as switches or amplifiers. These elements, when combined in various configurations, enable the operation of the electronic devices we use daily.

4. 2. 1. Basic Components
- Resistors

In electronics, a resistor (R) is a component whose function is to limit the flow of electric current within a circuit. Its purpose is to regulate the amount of current (I) flowing through other components, protecting them and ensuring the proper functioning of the circuit.

35

The value of the resistor is indicated by color bands printed on the component itself. These color combinations allow you to identify the resistance value in ohms, following the pattern established in the following table:

COLOR | BAND 1 | BAND 2 | BAND 3 | MULTIPLIER | TOLERANCE
Black | 0 | 0 | 0 | 1 Ω | -
Brown | 1 | 1 | 1 | 10 Ω | ± 1%
Red | 2 | 2 | 2 | 100 Ω | ± 2%
Orange | 3 | 3 | 3 | 1 kΩ | -
Yellow | 4 | 4 | 4 | 10 kΩ | -
Green | 5 | 5 | 5 | 100 kΩ | ± 0.5%
Blue | 6 | 6 | 6 | 1 MΩ | ± 0.25%
Purple | 7 | 7 | 7 | 10 MΩ | ± 0.10%
Gray | 8 | 8 | 8 | - | ± 0.05%
White | 9 | 9 | 9 | - | -
Gold | - | - | - | - | ± 5%
Silver | - | - | - | - | ± 10%

36
Keep in mind that there are resistors with 3 color bands (Band 1 and Multiplier, in addition to Tolerance), others with 4 color bands (Band 1, Band 2, and Multiplier, along with Tolerance), and even some with 5 bands. The Tolerance refers to the margin of error between the actual resistance value and the value indicated by the color bands.
- Light Emitting Diodes (LEDs)

An LED (Light Emitting Diode) is a type of diode with the unique characteristic of being able to emit light. A diode is an electronic component that allows current to flow in only one direction.

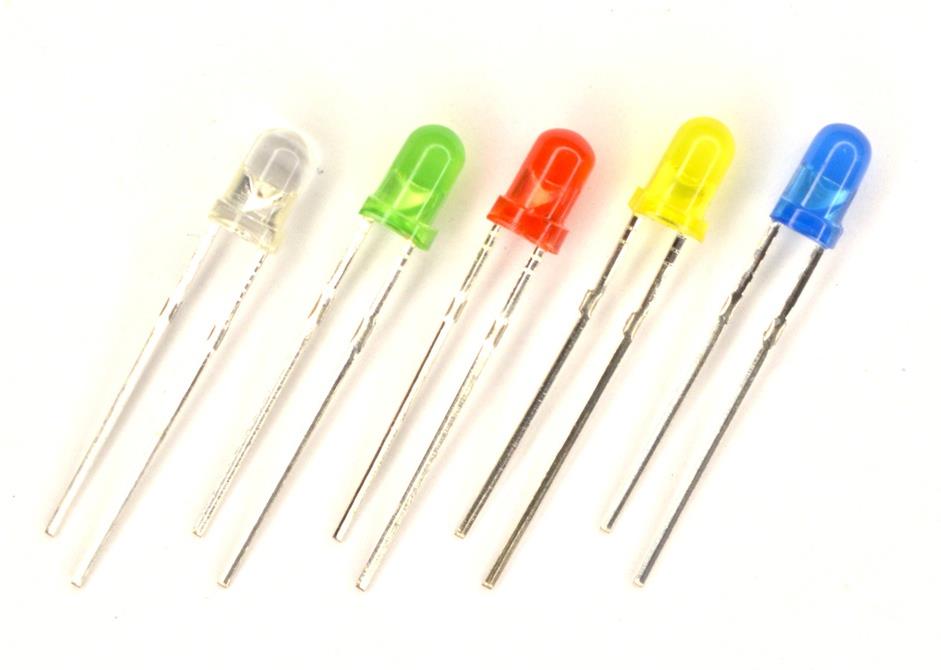
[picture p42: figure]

It consists internally of a semiconductor material with a p-n junction. Therefore, when it is forward biased, meaning the anode has a higher voltage than the cathode, the diode conducts electricity; when it is reverse biased, it blocks the flow of current. This operating principle of the diode makes it somewhat similar to a voltage-controlled switch. The LED indicates the polarity of the connection at a glance by the size of its connection leads. The longer lead corresponds to the anode (positive), while the shorter lead is the cathode (negative). In the case of the LED, when it conducts electricity, its semiconductor material releases energy in the form of photons, which causes it to emit light.

37

When an LED conducts electricity, it offers very little resistance to the flow of current, which means the power supply will provide as much current as possible uncontrollably, effectively creating a short circuit that poses a significant risk of burning out the LED. To prevent this, we should always connect a resistor of appropriate value (typically 220 ohms or higher) in series with the LED. This way, we can control the current flow and avoid damaging the LED.

- Capacitors

A capacitor is an electronic component that stores energy in the form of electric charge. It consists of two conductive plates separated by an insulating material called a dielectric. When a voltage is applied across the plates, charge accumulates on them, creating an electric field.

38

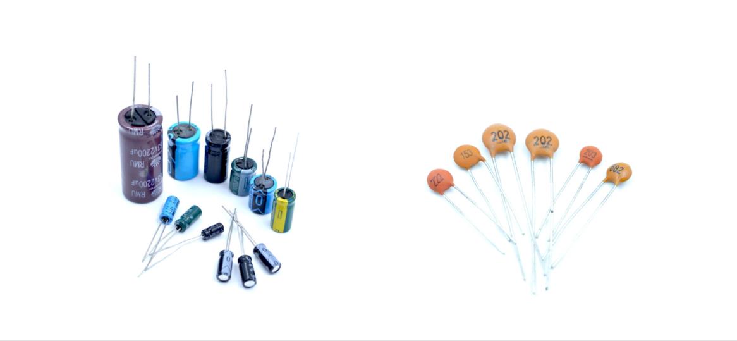
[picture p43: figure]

Capacitors are used in various applications, such as in filters, power supplies, timing circuits, and for smoothing electrical signals. Their ability to store and release energy quickly makes them essential in the design of electronic circuits. Capacitors are measured in farads (F), although smaller units like microfarads (µF) and nanofarads (nF) are commonly used.

4. 2. 2. Powering a Circuit

Powering an electronic circuit refers to the process of providing the necessary energy for the circuit to function correctly. This energy can come from various sources, such as batteries, power adapters, solar panels, or mains power supplies. The key aspects related to powering an electronic circuit are:

- Voltage (Tension): It is the force that drives electrons through the circuit. Each electronic component has a specific voltage range it requires to operate. For example, some microcontrollers operate at 5V, while others may need 3.3V.
- Current (Amperage): It is the amount of electrons flowing through the circuit. The power supply must be capable of providing sufficient current to meet the needs of all the components in the circuit.

39
- Stability: The power supply must be stable and constant to avoid fluctuations that could damage electronic components or affect their performance. This is especially important in sensitive circuits.
- Regulation: Some circuits require a specific and constant voltage, so voltage regulators are used to maintain the voltage at the appropriate level, regardless of variations in load or power supply.
- Types of Power Supply: Circuits can be powered by direct current (DC), such as that provided by batteries, or alternating current (AC), like that obtained from the electrical grid. Some circuits may require a converter to transform alternating current into direct current.
4. 2. 3. Configuration of Components in a Circuit

In electronics, components in a circuit can be connected in various ways, and each configuration affects the behavior of the circuit. The most common configurations are series, parallel, and mixed.

In a series configuration, components are connected one after another, forming a single path for the current. This means that the same current flows through all components.

40
In a parallel configuration, components are connected so that each one forms its own path for the current.

In a mixed configuration, components are connected in a combination of series and parallel. This setup allows for greater flexibility in circuit design and is used to meet specific voltage and current requirements.

4. 2. 4. Sensors

A sensor is a device that detects changes in the environment and converts that information into an electrical signal or data that can be interpreted by an electronic system. Sensors are essential in a wide range of applications, from automation and robotics to measurement and monitoring devices.

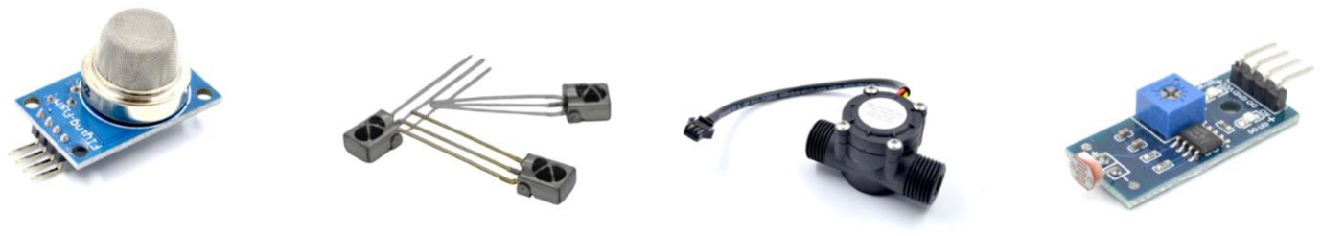
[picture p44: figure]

Sensors are capable of detecting different types of stimuli, such as light, temperature, pressure, humidity, motion, sound, and more. Each type of sensor is designed to measure a specific magnitude, acting as transducers, meaning they convert one form of energy (such as thermal, mechanical, or luminous energy) into an electrical signal that can be processed by other devices, like microcontrollers. The generated signal can be either analog (a continuous variation, such as a voltage) or digital (a discrete value, such as "yes" or "no").

41

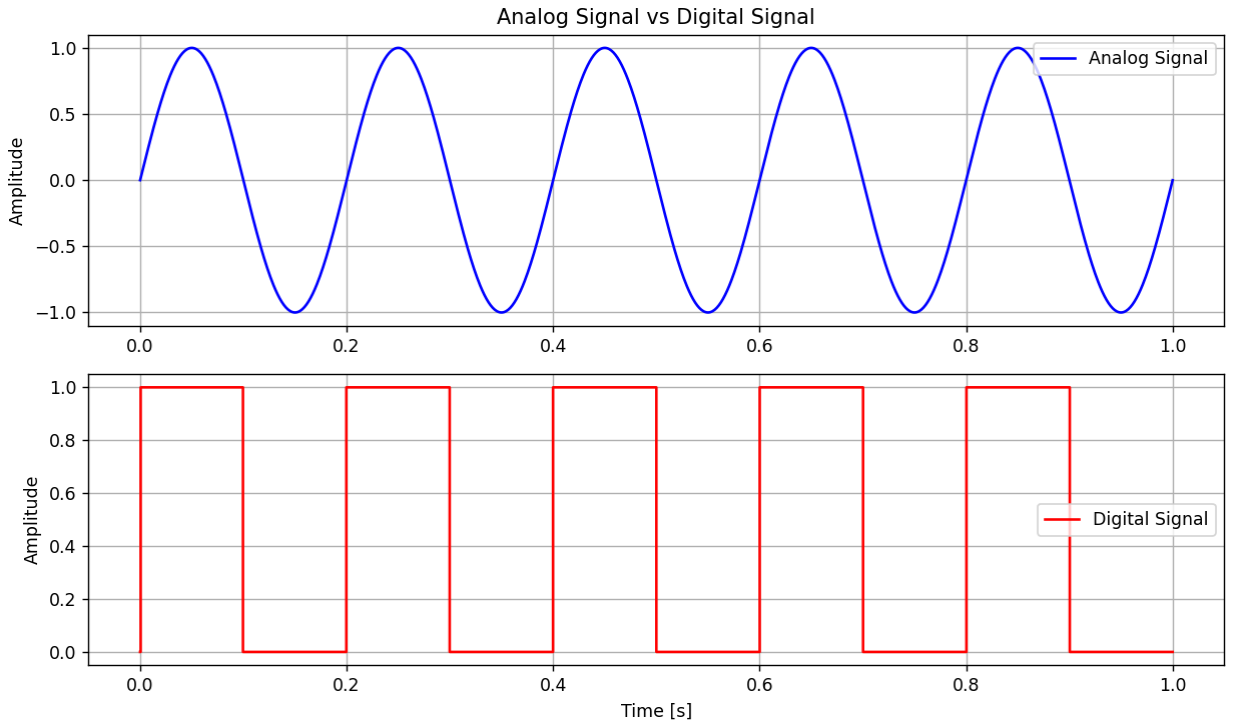
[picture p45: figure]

Sensors are used in a wide range of applications, such as in home automation to control the climate of a house, in cars for security systems, in wearable devices to monitor health, and in industry for process control. For example, a DHT-11 or DHT-22 is a type of temperature sensor that provides measured values with a digital signal, while a photoresistor is a type of sensor that varies its electrical resistance based on the amount of light incident upon it, allowing for an analog signal to be obtained.

42
4. 2. 5. Actuators

An actuator is a device that converts a control electrical signal into movement or a physical action within a system. Actuators work in conjunction with sensors in control systems. While sensors detect and measure changes, actuators respond to that information to perform actions and modify the environment or the controlled system through signals that can be either analog or digital, sent by a control system such as a microcontroller or a computer. These signals indicate to the actuator what task it should perform, whether it's opening a valve, moving a robotic arm, or rotating a motor.

There are different types of actuators:

- Electric Actuators: They use electrical energy to generate movement, such as electric motors, solenoids, and servomotors.
- Hydraulic Actuators: They operate using fluid pressure to move objects, commonly used in systems requiring significant force, such as heavy machinery.
- Pneumatic Actuators: They employ compressed air to generate movement, often found in industrial applications and automation systems.

43

Actuators are essential in a wide variety of applications. In robotics, for example, they enable the movement of arms or wheels, while in home automation, they control elements such as blinds or automatic doors. They are also present in automobiles, where they manage the movement of seats or the opening of valves.

### 4. 3. Breadboard

A breadboard is a type of "workspace" for creating electronic circuits. It is a board filled with small holes where you can insert various components such as resistors, LEDs, wires, etc. These holes are internally connected in such a way that when a component is placed in one of them, it automatically connects with other holes following an established pattern.

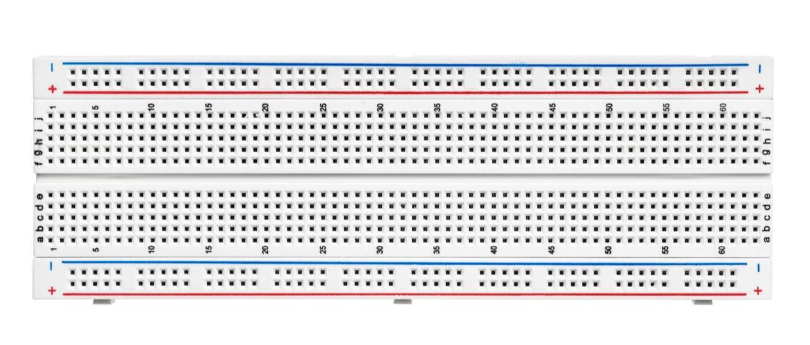
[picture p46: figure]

44
The breadboard allows you to experiment with different circuit configurations without the need to solder the components permanently. You can easily move, replace, or remove elements without causing any damage.

The image shows how the holes in a breadboard are internally connected. The copper strips inside allow certain groups of holes to be connected to each other. In this case, the horizontal lines, which are typically the power rails located along the edges of the board, are electrically connected along their entire length. This means that any component or wire inserted into those holes will share the same power or ground connection.

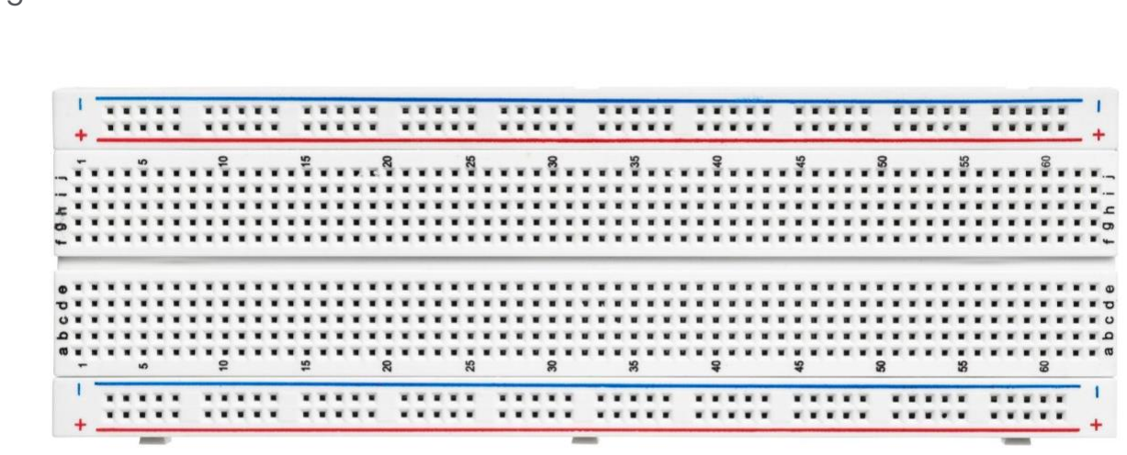
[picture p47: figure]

45
On the other hand, the groups of vertical lines found in the central area of the breadboard are also electrically connected to each other. These connection groups are isolated from one another, but within each group, the components you place will share the same connection, making it easier to create complex circuits without the need for soldering. This internal connection design allows for easy manipulation and modification of experimental circuits on the breadboard.
4. 3. 1. Activities with a Breadboard

In this first activity, the objective is to learn how to use the breadboard and understand the flow of current in a simple circuit. To achieve this, you can use the VIN and GND pins to power the circuit on the breadboard with the side power rails, noting that VIN is the positive terminal and GND is the negative. You will then need an LED as a visual indicator of power and a resistor to limit the current. Connect the LED in series with the resistor in any area of the breadboard, ensuring that the LED diode is connected in the correct orientation. Once the circuit is complete and the ESP32 is connected to the computer, the LED should light up, indicating that current is flowing correctly.

As a review element, could you tell me the value of the resistor used in the schematic?

46
In this next activity, the goal is to connect two LEDs in series along with their current-limiting resistor. Connect the negative terminal of one LED to the positive terminal of the next, and then place the resistor, connecting both ends of the circuit to the power rails. Be sure to pay attention to the orientation of both LEDs.

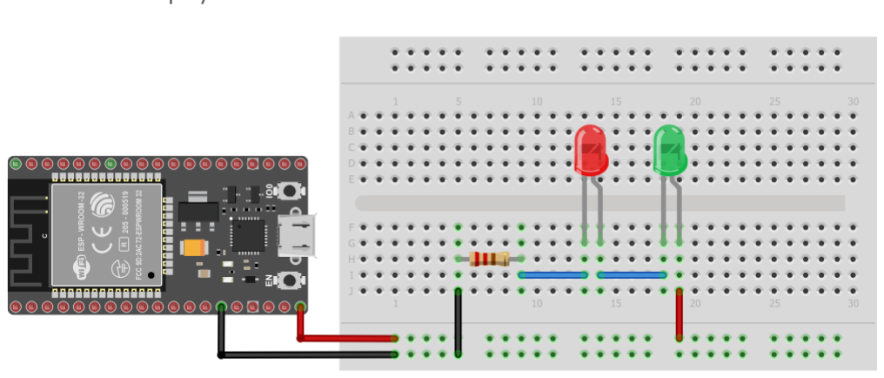
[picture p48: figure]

To continue practicing with the breadboard, we will set up the same two LEDs from the previous exercise, but in parallel, each with different values of current-limiting resistors.

Could you tell me the values of the resistors used this time by looking at the schematic?

47
4. 3. 2. Voltage Divider

A voltage divider is a very simple and useful circuit that allows you to obtain a fraction of the input voltage using two resistors connected in series. It is commonly used in applications where it is necessary to reduce a voltage to a level that can be used by other components.

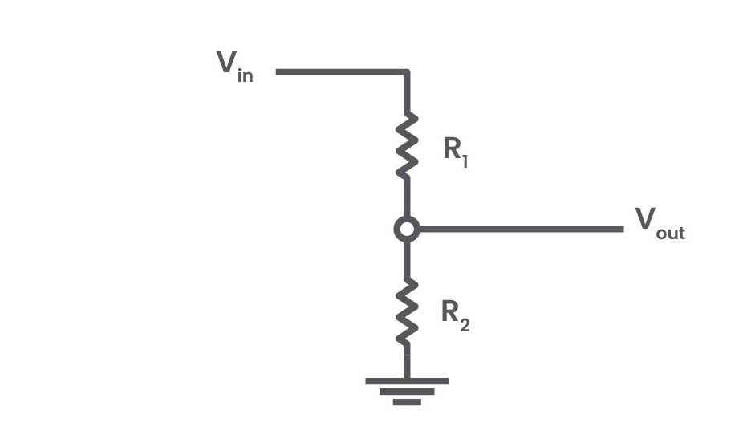
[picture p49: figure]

When two resistors are connected in series to a voltage source, the current that flows through them is the same, but the voltage is divided between the resistors according to their values. The voltage divider takes advantage of this property to "divide" the input voltage into a smaller portion. The voltage at the output of the divider can be calculated using the following expression:

48
If you have a 5V source and use two resistors in series of 1 kΩ (R1) and 2 kΩ (R2), the output voltage of the voltage divider can be calculated as follows:

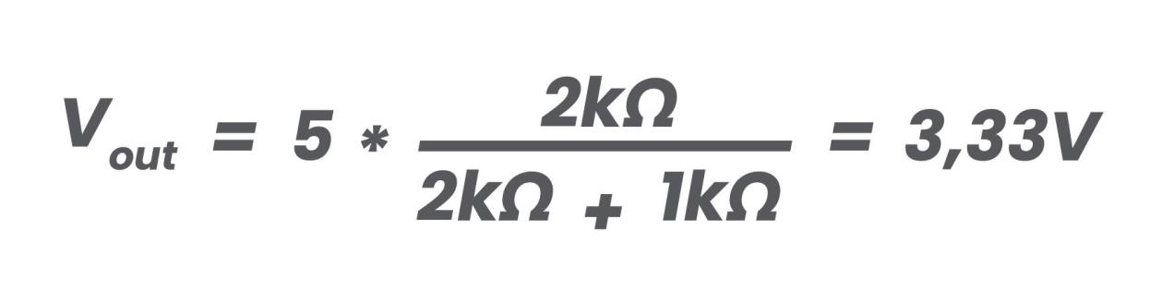
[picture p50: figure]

4. 3. 3. Activities with Voltage Dividers

To practice the concept of a voltage divider, set up two 1 kΩ resistors in series on the breadboard and use the ESP32 again to power the circuit (remember that VIN is the positive supply and GND is the negative), as shown in the following schematic. Measure the voltage at the midpoint between the two resistors and verify that it matches the value calculated using the voltage divider formula.

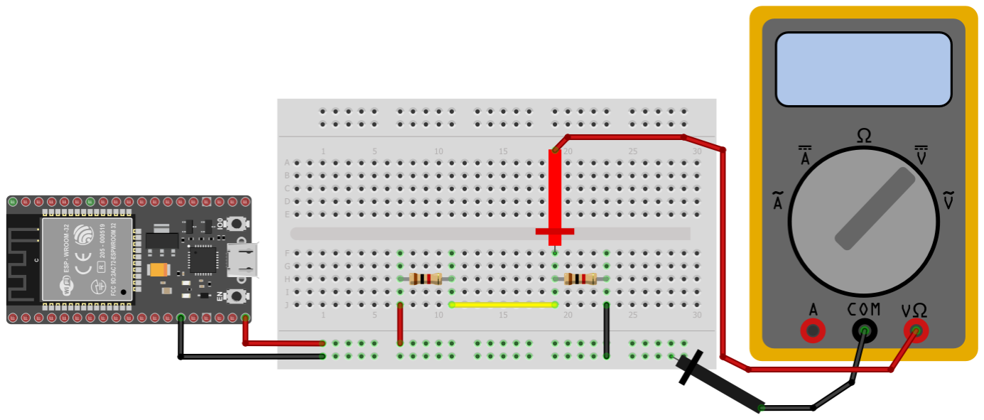
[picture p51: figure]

49
Now create a circuit with a voltage divider using a 2 kΩ resistor (R1) and a 3 kΩ resistor (R2) connected in series to the ESP32's power supply. Calculate the output voltage of the divider and verify its accuracy by measuring the voltage at the indicated point. Below is the schematic for the voltage divider for the exercise.

## 5. ASSEMBLY OF THE 3-IN-1 DEMONSTRATOR

The assembly of the 3x1 Demonstrator will be carried out modularly, addressing each section separately in the corresponding sections of this guide. This approach aims to simplify the process and enhance understanding, ensuring that the assembly is clear and accessible for those undertaking it. Each step is designed to guarantee a functional and effective outcome, even for individuals with no prior experience in assembling demonstrators.

One of the main goals of this project is to promote the autonomy of educational institutions, enabling them to create their own demonstrators if they have 3D printers on-site. For this reason, we have made the necessary printing files available for the fabrication of the components, which can be downloaded via the following link: 3D Printing Files. (https://drive.google.com/drive/folders/1F19XPgi768G87Ds_K66nvXBx-3E4KJT6) With this tool, we aim to empower educational institutions to independently and efficiently integrate these demonstrators into their activities.

50

### 5.1. List of Materials

- 1 x ESP32 DEVKIT V1 with 30 pins
- 2 x Mini breadboards with 170 tie-points
- 1 x DHT11 module, maximum width 14 mm, with or without built-in LED
- 10/12* x Male-to-male jumper wires, 10 cm
- 5 x Male-to-male jumper wires, 20 cm
- 3 x Male-to-female jumper wires, 10 cm
- 10 x Male-to-female jumper wires, 20 cm
- 5 x 1k ohm resistors
- 1 x Capacitor, 100nF or 1uF
- 3 x Colored LEDs (preferably Red, Green, and Blue)
- 1 x Solar panel, maximum dimensions: 45 mm x 60 mm
- 1 x Water level sensor, 6 cm x 2 cm
- 1 x 5V DC motor, maximum dimensions: 28 mm diameter and 45 mm length
- 1 x SG-90 Servo motor
- 1 x Voltage detector
- 2 x Photoresistors standalone GL5528
- 1 x 6203 bearing, either ZZ or 2RS type: 40 mm outer diameter, 17 mm inner diameter, and 12 mm height
- 3 x Wooden dowels: 8 mm diameter and 40 mm length
- 1 x Motor gear: 2 mm inner diameter, 10 teeth, and 5 mm height
- 1 x Data transfer cable USB to microUSB
- 1 x Aluminum tape, 5 cm wide
- 1 x Double sided tape, 3 cm de wide

* If the Motor DC doesn’t come with wires, you will need 12 male-to-male jump wires of 10 cm.

Tools you might need:

- Soldering iron: if the Motor DC or the Solar Panel don’t come with wires.
- Flat head screw driver 2 mm: for the voltaje sensor.

51

### 5. 2. Assembly of the Water and Solar Demonstrator

5. 2. 1. Electronic Assembly (Water Component)

We will begin by assembling the water collector. To complete this assembly, you will need the following materials:

1 x DHT-11 Sensor | 3 x 1 kΩ Resistors
Responsible for measuring ambient temperature and humidity. | Used to limit the current flowing through LED diodes.

3 x Colored LEDs (Preferably Red, Green, and Blue)

### 1 x Dupont Cables

(Male-Male) 10cm

Used as visual indicators of the measured temperature range.

Necessary for making connections between the different components on

52
the breadboard.

### 2 x Mini Breadboard

### 6 x Dupont Cables

(Male-Female) 20cm

Component necessary to connect the microcontroller board to the different components.

Necessary for making connections between the different components on the breadboard.

1 x Water level sensor | 1 x ESP32 DEVKIT V1 (30 pins)
Used to measure the water level in the tank. | Responsible for executing the programming that controls the operation of the electronics.

The objective of the assembly is to obtain the values of ambient temperature and humidity, and based on the temperature value, to light up a specific LED as indicators of danger for high or low temperatures. In this way, if the temperature is below 20ºC,

53
the Blue LED will light up; if it is above 25ºC, the Red LED will light up; and if it is between those values (between 20 and 25ºC), the Green LED will light up.
The first step is to place the ESP32 board on two small breadboards to have enough space to connect the components we will need later. Below, you can see the result:

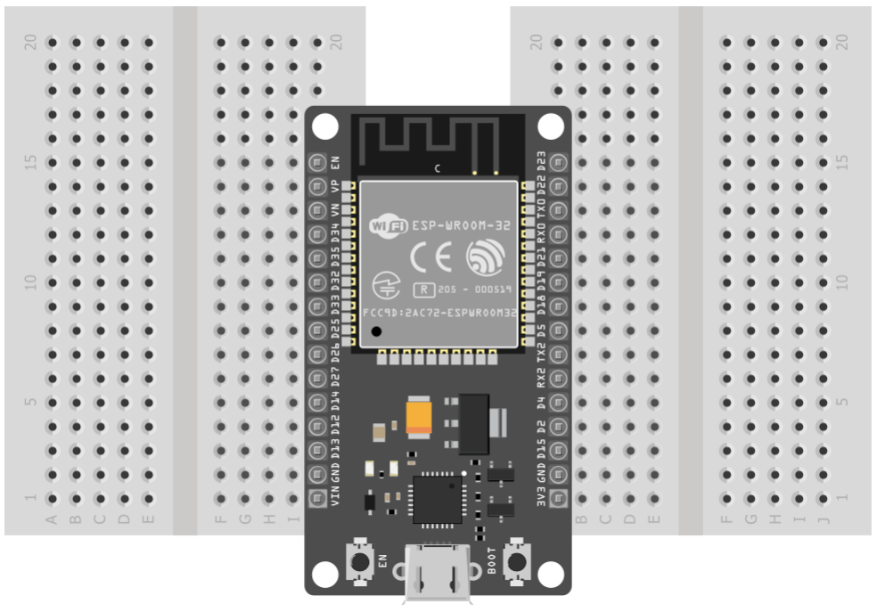
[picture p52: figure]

Once we have the microcontroller placed on the two breadboards, we will start connecting the colored LEDs with their current-limiting resistors. We will begin by placing the Blue LED and one of the 1 kΩ resistors in series. We will connect the positive of the LED to pin D5 and use any GND pin to connect the negative of the circuit. Below, you can see the indicated assembly.

Note: The LED diode indicates the polarity of the connection at a glance by the length of its leads. The longer lead corresponds to the anode, or positive, and the shorter one is the cathode, or negative. In the diagram, the longer lead is the one connected in series with the resistor.

54

To verify the correct functioning of the assembly, we can upload the following code to the ESP32:

#define ledPin1Cold 5 // Define the pin where the Blue LED is connected

// Initialization block

void setup() {

// We configure the operating mode of the LED pin as an output

pinMode(ledPin1Cold, OUTPUT);

}

// Main loop of the code

void loop() {

digitalWrite(ledPin1Cold, LOW); // We turn off the LED

delay(1000); // We wait 1 second = 1000 milliseconds

digitalWrite(ledPin1Cold, HIGH); // We turn on the LED

delay(1000); // We wait 1 second

}

55
This small program makes the Blue LED blink, changing its state between on and off every second. If it does not work correctly, check that the LED is oriented properly (remember that the longer lead is the positive terminal, while the shorter one is the negative) and connected appropriately with the current-limiting resistor.

The next step in the assembly will be to add a second LED. This time, we will place and connect the Green LED to pin D18 with its resistor. You can see the indicated assembly schematic in the following image.

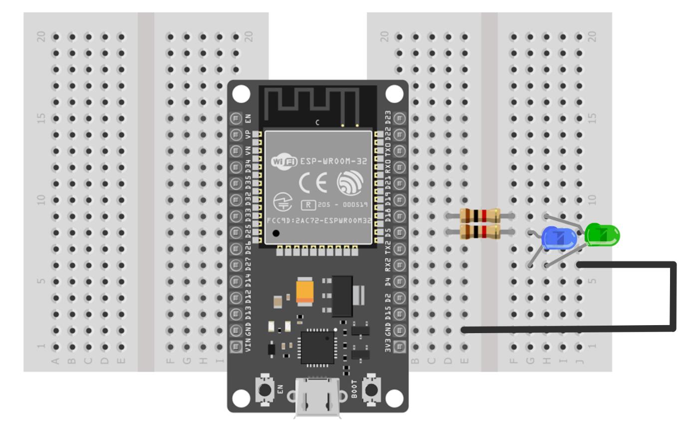
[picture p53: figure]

Let's verify that the assembly is correct again. We will use the code below to check that the new LED is also properly placed.

56

#define ledPin1Cold 5 // Define the pin where the Blue LED is connected

#define ledPin2Good 18 // Define the pin where the Green LED is connected

// Initialization block

void setup() {

// We configure the operating mode of the LEDs pins as outputs

pinMode(ledPin1Cold, OUTPUT);

pinMode(ledPin2Good, OUTPUT);

}

// Main loop of the code

void loop() {

digitalWrite(ledPin1Cold, LOW); // We turn off the Blue LED

digitalWrite(ledPin2Good, LOW); // We turn off the Green LED

delay(1000); // We wait 1 second = 1000 milliseconds

digitalWrite(ledPin1Cold, HIGH); // We turn on the Blue LED

digitalWrite(ledPin2Good, HIGH); // We turn on the Green LED

delay(1000); // We wait 1 second

}

As you can see, the objective of the code remains the same: to turn both LEDs on and off, changing their state every second. If the Blue and Green LEDs are changing states correctly, we can consider the current assembly valid and proceed to the next step.

To complete the assembly of the colored LEDs needed to fulfill the established objective for this part of the Demonstrator, we need to connect the last LED, which is Red, to pin D19. Proceed to assemble the LED diode and the corresponding last resistor, as shown in the following image.

57

We will check that it is correct by using the same programming as in the previous cases, generating a blink in all three colored LEDs. The code for this is as follows:

#define ledPin1Cold 5 // Define the pin where the Blue LED is connected

#define ledPin2Good 18 // Define the pin where the Green LED is connected

#define ledPin3Heat 19 // Define the pin where the Red LED is connected

// Initialization block

void setup() {

// We configure the operating mode of the LEDs pins as outputs

pinMode(ledPin1Cold, OUTPUT);

pinMode(ledPin2Good, OUTPUT);

pinMode(ledPin3Heat, OUTPUT);

}

// Main loop of the code

void loop() {

digitalWrite(ledPin1Cold, LOW); // We turn off the Blue LED

digitalWrite(ledPin2Good, LOW); // We turn off the Green LED

digitalWrite(ledPin3Heat, LOW); // We turn off the Red LED

58

delay(1000); // We wait 1 second = 1000 milliseconds

digitalWrite(ledPin1Cold, HIGH); // We turn on the Blue LED

digitalWrite(ledPin2Good, HIGH); // We turn on the Green LED

digitalWrite(ledPin3Heat, HIGH); // We turn on the Red LED

delay(1000); // We wait 1 second

}

The next step is to add and connect the DHT11 sensor to pin D32, either as an individual component or on a module. Below is the assembly completed so far along with the connections for the DHT11 sensor.

Note: Make sure that the GND and VCC connections of the DHT11 sensor match the actual pinout of the component, as they may differ from what is shown in the diagram.

59
We will now check the correct functioning of the DHT-11 sensor. Below is a test code for the entire assembly completed for this part of the project. Upload the program, and you will see that, in addition to the colored LEDs blinking as they have done so far, the ESP32 board will send the obtained measurements of ambient temperature (in °C) and relative humidity (in %) to the Serial Monitor every couple of seconds (you can see the button to open it in the following image).

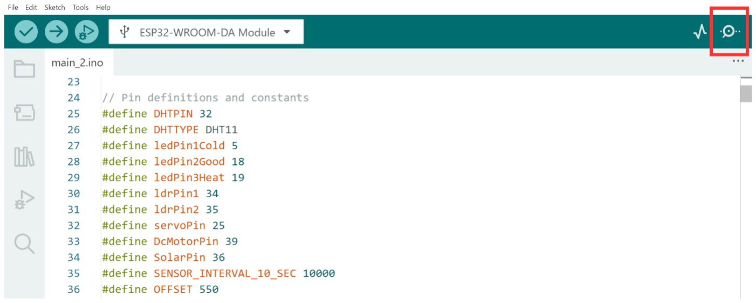
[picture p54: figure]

#include <DHT.h> // We include the necessary library to control DHT.

#define ledPin1Cold 5 // Define the pin where the Blue LED is connected

#define ledPin2Good 18 // Define the pin where the Green LED is connected

#define ledPin3Heat 19 // Define the pin where the Red LED is connected

#define DHTPIN 32 // Define the pin to which the DHT is connected

#define DHTTYPE DHT11 // Define the type of DHT sensor to use

// Define the type of DHT sensor to be usedCreate an object of type DHT with the corresponding

configuration

DHT myDHT11(DHTPIN, DHTTYPE);

// Initialization block

void setup() {

// We configure the operating mode of the LEDs pins as outputs

pinMode(ledPin1Cold, OUTPUT);

pinMode(ledPin2Good, OUTPUT);

pinMode(ledPin3Heat, OUTPUT);

// Initialize the Serial monitor

Serial.begin(115200);

60

// Initialize the DHT sensor

myDHT11.begin();

}

// Main loop of the code

void loop() {

digitalWrite(ledPin1Cold, LOW); // We turn off the Blue LED

digitalWrite(ledPin2Good, LOW); // We turn off the Green LED

digitalWrite(ledPin3Heat, LOW); // We turn off the Red LED

delay(1000); // We wait 1 second = 1000 milliseconds

digitalWrite(ledPin1Cold, HIGH); // We turn on the Blue LED

digitalWrite(ledPin2Good, HIGH); // We turn on the Green LED

digitalWrite(ledPin3Heat, HIGH); // We turn on the Red LED

delay(1000); // We wait 1 second

// We obtain the DHT sensor measurements

float temperature = myDHT11.readTemperature();

float humidity = myDHT11.readHumidity();

// We show the values per monitor Serial

Serial.print("Temperature: ");

Serial.println(temperature);

Serial.print("Humidity: ");

Serial.println(humidity);

}

With the monitor open, make sure that the dropdown located furthest to the right on the Monitor is set to "115200". Now you will be able to see the data sent by the ESP32 from the DHT-11 constantly and verify that the assembly up to this point is functioning correctly.

The next component to be added is the water level sensor module. Connect the sensor to pin VN. In the following image you can see how the assembly will look like:

61

Now we are going to verify the operation of the water level sensor by constantly reading and displaying the measured value of the sensor on the serial monitor:

//Water sensor calibration

const int WaterSensorPin = 39; // Analog Value from VN PIN

void setup() {

Serial.begin(115200);

}

void loop() {

int sensorValue; // Variable to store sensor values

sensorValue = analogRead(WaterSensorPin); // Read the value from the sensor

Serial.println(sensorValue); // Print value in serial monitor

delay(100);

}

62

63
5. 2. 2. Electronic Assembly (Solar Component)

We will begin by assembling the solar component. To complete this assembly, you will need the following materials:

1 x SG-90 Servo Motor | 2 x Photoresistors -
Used to move the solar demonstrator and orient it toward sunlight. | Used to measure the level of received light intensity.
2 x 1 kΩ Resistors | 9 x Dupont Cable (Male-Male) 10 cm
Used only with the independent LDRs to assemble a voltage divider controlled by light intensity. | Necessary for making connections between the different components on the breadboard.

64

### 5 x Dupont cable

(Male-Male) 20cm

### 3 x Dupont cable

(Male-Female) 10cm

Necessary for making connections between the different components on the breadboard.

Necessary for making connections between the different components on the breadboard.

### 4 x Dupont cable

(Male-Female) 20cm | 1 x Voltage sensor
Necessary for making connections between the different components on the breadboard. | Used alongside the solar panel to detect sunlight.

### 1 x Solar Panel

Used to detect sunlight.

65
The objective of the assembly will be to determine the orientation of the incidence of sunlight with the LDRs and rotate the Demonstrator to maximize the amount of sunlight hitting the panel.

The assembly of the solar component will begin from the last assembly seen in the previous section. In this assembly, an LDR and a resistor will be added in series, forming a voltage divider controlled by light intensity. To obtain the value from the sensor, the digital output will be connected to pin D34 of the ESP32. The assembly can be seen below:

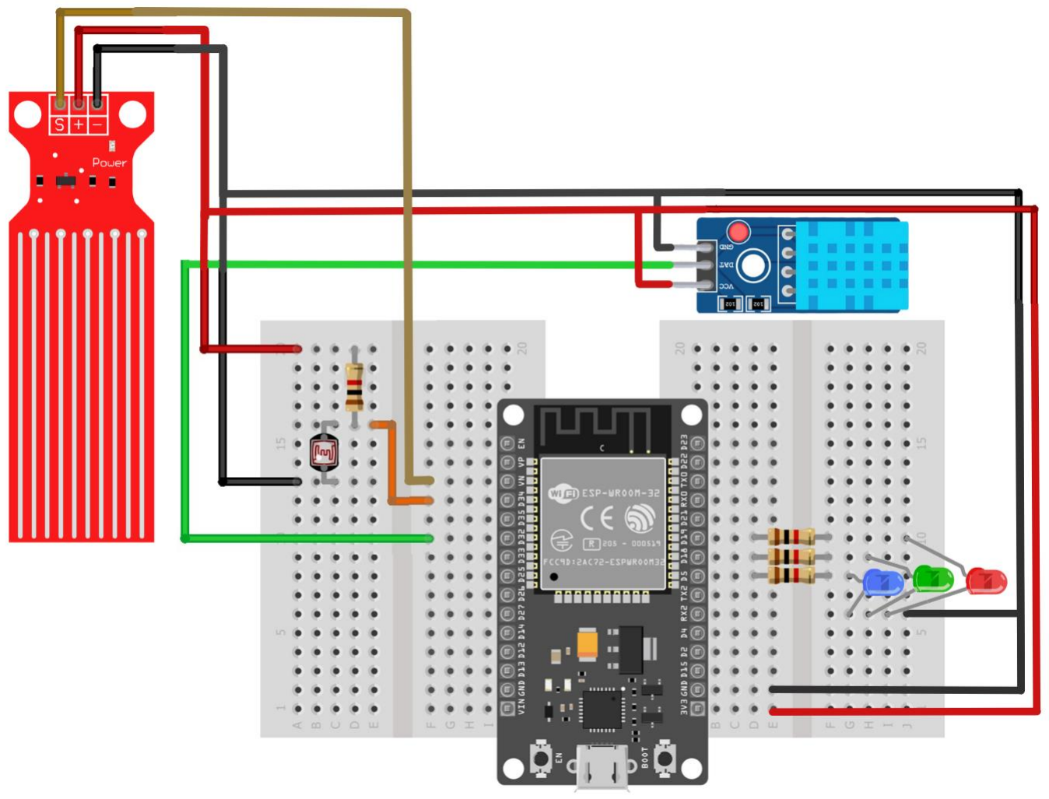
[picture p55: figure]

To check the functionality of the new elements added to the assembly, we will use a code that only reads the LDR value to light up the Red LED with greater or lesser intensity based on the brightness measured by the photoresistor. You can see the code to upload below:

66

#define ldrPin1 34 // Define the pin to which the LDR is connected

// Initialization block

void setup() {

// Initialize the serial monitor

Serial.begin(115200);

}

// Main loop of the code

void loop() {

// We take the reading of the pin where the LDR is located.

int reading_ldr_1 = analogRead(ldrPin1);

// Display the value on the Serial monitor

Serial.print("Luminosity 1: ");

Serial.println(reading_ldr_1);

}

Next, the second LDR with its resistor should be added. To obtain the reading value from this sensor, the digital output will be used, as in the previous case, but this one will be connected to pin D35. Below, you can see the assembly with both LDRs for the current part of the Demonstrator.

67

Let's verify that the connections have been made correctly using the following code, which is very similar to the previous one but displays the measurement values from both photoresistors.

#define ldrPin1 34 // Define the pin to which the first LDR is connected

#define ldrPin2 35 // Define the pin to which the second LDR is connected

// Initialization block

void setup() {

// Initialize the serial monitor

Serial.begin(115200);

}

// Main loop of the code

void loop() {

// We take the readings of the pins where the LDRs are located

68

int reading_ldr_1 = analogRead(ldrPin1);

int reading_ldr_2 = analogRead(ldrPin2);

// We display the first value on the Serial monitor

Serial.print("Luminosity 1: ");

Serial.println(reading_ldr_1);

// We display the second value on the Serial monitor

Serial.print("Luminosity 2: ");

Serial.println(reading_ldr_2);

}

The next component to be added to the assembly is a servo motor. This will be connected to both power rails (the red wire to the positive and the black wire to the negative), and the yellow wire (which is the control signal) will be connected to pin D25.

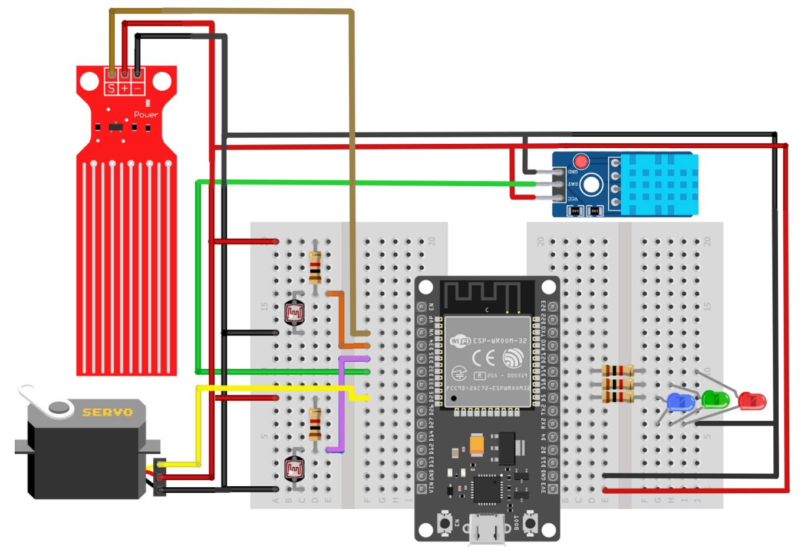
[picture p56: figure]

We will check the operation of the servo motor by uploading the following code to the ESP32, which sweeps the servo between the positions of 0º, 90º, and 180º in a loop repeatedly.

69

#include <ESP32Servo.h> // Include the necessary library to control the servomotor

#define servoPin 25 // Define the pin where the servomotor is connected

// We create an object of type Servo to control it

Servo myServo;

// Initialization block

void setup() {

// We associate the servo we created to the pin where it is connected

myServo.attach(servoPin);

// We place the servo in an initial position of 0º

myServo.write(0);

}

// Main loop of the code

void loop() {

myServo.write(0); // We move the servomotor to 0º

delay(1000); // We wait 1 second = 1000 milliseconds

myServo.write(90); // We move the servomotor to 90º

delay(1000); // We wait 1 second

myServo.write(180); // We move the servomotor to 180º

delay(1000); // We wait 1 second

}
Note: Attach the helix to the servo. Screws are not needed to secure it.

The last component we will connect to the ESP32 will be a voltage detector. This module should be powered through both power rails (Vcc and GND). The signal line will be connected to pin VP.

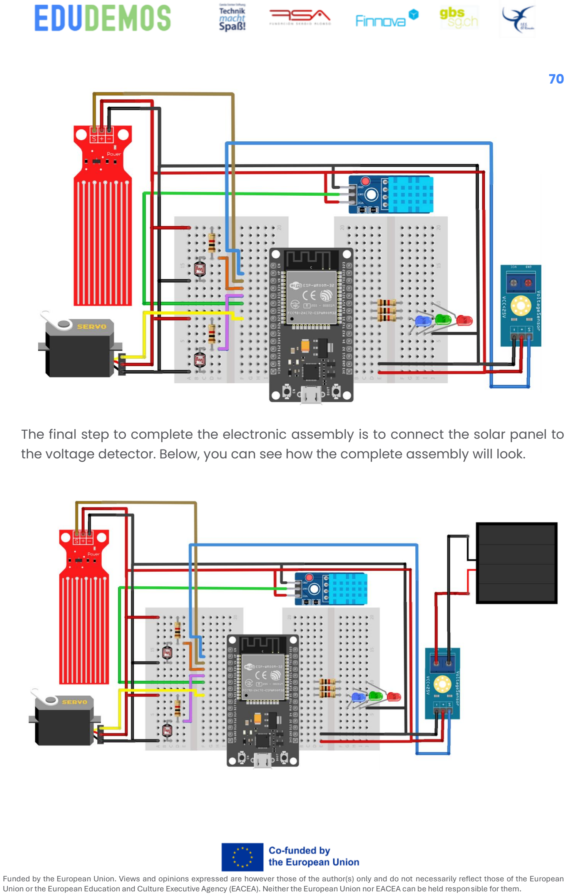
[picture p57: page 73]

70

The final step to complete the electronic assembly is to connect the solar panel to the voltage detector. Below, you can see how the complete assembly will look.

71

We will check the functionality of the complete solar detector by using the following code, which simply reads the signal from the voltage detector module and turns on the Blue LED if it detects voltage.

#define ledPin1Cold 5 // Define the pin where the Blue LED is connected

#define detectorPin 36 // Define the pin where the Voltage Detector is connected

// Initialization block

void setup() {

// We configure the operating mode of the LED pin as an output

pinMode(ledPin1Cold, OUTPUT);

}

// Main loop of the code

void loop() {

// We take the reading of the Detector Module

bool tension_detectada = digitalRead(detectorPin);

// We check if there is tension or not

if(tension_detectada) { // Yes, there is tension

digitalWrite(ledPin1Cold, HIGH); // We turn on the Blue LED

} else { // No tension

digitalWrite(ledPin1Cold, LOW); // We turn off the Blue LED

}

}

Below is a test code to verify that all the sensors are getting readings and working correctly:

//include the necessary libraries #include <ESP32Servo.h>

#include "DHT.h"

// Pin definitions and constants

#define ldrPin1 34 // set ldr 1 Analog input pin of East ldr as an integer

#define ldrPin2 35 // set ldr 2 Analog input pin of West ldr as an integer

72

#define DHTPIN 32

#define DHTTYPE DHT11

#define ledPin1Cold 5

#define ledPin2Good 18

#define ledPin3Heat 19

#define SolarPin 36

// Global variables

DHT dht(DHTPIN, DHTTYPE);

Servo myservo;

int valldr1 = 0 ;

int valldr2 = 0 ;

int averageLdrValue = 0;

int servopos = 90; // initial position of the Horizontal movement controlling servo

motor

int tolerance = 20; // allowable tolerance setting - so solar servo motor isn't

constantly in motion

float lastMicrovolts = 0;

const int WaterSensorPin = 39; // Analog Value from VN PIN

int sensorValue; // Variable to store sensor values

void setup(){

Serial.begin(115200);

analogReadResolution(12); // ESP32 has a 12-bit ADC

analogSetAttenuation(ADC_11db); // Set attenuation for higher sensitivity

pinMode(4, INPUT);

dht.begin(); // Start the DHT sensor

pinMode(ledPin1Cold, OUTPUT);

pinMode(ledPin2Good, OUTPUT);

pinMode(ledPin3Heat, OUTPUT);

myservo.attach(25); // attaches the servo on digital pin 2 to the horizontal movement

servo motor

pinMode(ldrPin1, INPUT); //set East ldr pin as an input

pinMode(ldrPin2, INPUT); //set West ldr pin as an input

myservo.write(servopos); // write the starting position of the horizontal movement

servo motor

delay(1000); // 1 second delay to allow the solar panel to move to its staring position

before commencing solar tracking

}

73

void loop(){

Serial.println("----------------------------- Measured Solar (V) ------------------

---------- ");

int solarVoltagedV = analogRead ( SolarPin); //dV

int solarVoltage = solarVoltagedV * 10;

Serial.print("Voltage of Solar Panel: ");

Serial.println(solarVoltage);

// Calculate voltage

float voltage = (solarVoltage / 4095.0) * 3.3; // For 12-bit ADC (0-4095)

Serial.print("Measured voltage (V): ");

Serial.println(voltage); // Display the measured voltage

// Convert to microvolts

float microvoltsSolar = voltage * 1000000.0;

Serial.print("Input voltage (µV): ");

Serial.println(microvoltsSolar);

// Apply a minimum threshold to filter noise

const float threshold = 10.0; // Threshold in microvolts

if (microvoltsSolar < threshold) {

microvoltsSolar = 0;

}

// Check if the microvolts value has changed

if (microvoltsSolar != lastMicrovolts) {

Serial.print("Send voltage: ");

Serial.print(microvoltsSolar, 2); // Display with 2 decimal places

Serial.println(" µV");

// Update the last microvolts value

lastMicrovolts = microvoltsSolar;

}

Serial.println("----------------------- Measured Temperature / Humidity -----------

------------ ");

// Read values from DHT sensor

float h = dht.readHumidity();

float t = dht.readTemperature();

// Check if readings are valid

if (isnan(h) || isnan(t)) {

74

Serial.println("Failed to read from DHT sensor!");

return;

}

// Print sensor values

Serial.print("Temperature: ");

Serial.print(t);

Serial.print(" °C, Humidity: ");

Serial.print(h);

Serial.print(" %");

// Example LED control based on temperature

if (t < 20) {

digitalWrite(ledPin1Cold, HIGH);

digitalWrite(ledPin2Good, LOW);

digitalWrite(ledPin3Heat, LOW);

Serial.println("Cold is HIGH");

} else if (t >= 20 && t < 25) {

digitalWrite(ledPin1Cold, LOW);

digitalWrite(ledPin2Good, HIGH);

digitalWrite(ledPin3Heat, LOW);

Serial.println("Good is HIGH");

} else {

digitalWrite(ledPin1Cold, LOW);

digitalWrite(ledPin2Good, LOW);

digitalWrite(ledPin3Heat, HIGH);

Serial.println("Heat is HIGH");

}

Serial.println("----------------------------- Measured Water Level ----------------

------------- ");

int sensorValue; // Variable to store sensor values

sensorValue = analogRead(WaterSensorPin); // Read the value from the soil moisture

sensor

//Check watersensor calibration first

if (sensorValue >= 2000) { //These value represents de max value given

sensorValue = 1980; //This value would return a 99% value

}

float waterlevel = (sensorValue*100)/2000 ; //Calculation to return the %

Serial.print("Water level: "); // Print value in serial monitor

Serial.print(waterlevel); // Print value in serial monitor

Serial.println(" %"); // Print value in serial monitor

75

Serial.println("----------------------------- Measured LDR and Servo --------------

--------------- ");

// Read LDR values

valldr1 = analogRead(ldrPin1); // read the value of ldr 1

valldr2 = analogRead(ldrPin2); // read the value of ldr 2

// Invert readings so low values mean darkness and high values mean light

averageLdrValue = (valldr1 + valldr2) / 2;

// Print readings for debugging

Serial.print("LDR 1: ");

Serial.print(valldr1);

Serial.print(" | LDR 2: ");

Serial.println(valldr2);

Serial.print("Average LDR: ");

Serial.println(averageLdrValue);

if((abs(valldr1 - valldr2) <= tolerance) || (abs(valldr2 - valldr1) <= tolerance)) {

//no servo motor horizontal movement will take place if the ldr value is within the

allowable tolerance

}else {

if(valldr1 > valldr2) // if ldr1 senses more light than ldr2

{

servopos = servopos+10; // decrement the 90 degree position of the horizontal servo

motor - this will move the panel position Eastward

}

if(valldr1 < valldr2) // if ldr2 senses more light than ldr1

{

servopos = servopos-10; // increment the 90 degree position of the horizontal motor -

this will move the panel position Westward

}

}

if(servopos > 180) {servopos = 180;} // reset the horizontal position of the motor to

180 if it tries to move past this point

if(servopos < 0) {servopos = 0;} // reset the horizontal position of the motor to 0 if

it tries to move past this point

myservo.write(servopos); // write the starting position to the horizontal motor

// Print the servo angle

Serial.print("Servo angle: ");

Serial.print(servopos);

delay(5000);

76

}
5. 2. 3. Mechanical Assembly of the Water and Solar Demonstrator

The elements that make up this demonstrator are as follows:

Element | Quantify | Description | Image
Base | 1 | It is the upper part that secures the moving components, such as the blades and the motor shaft. It provides stability and allows the system to operate smoothly, facilitating the correct transfer of energy from the blades to the generator.
Drawer | 1 | It is the base that connects the different sections of the device, providing structural support and ensuring proper alignment between the motor, the blades, and other essential components for its operation.
Water container | 1 | This part is capable of storing the water that falls into it.
Leaf | 8 | A sheet that allows liquids to enter the water collection container.

77
Small disc | 3 | It is a static component that does not move. Its primary function is to act as part of the structural support of the device, helping to maintain proper alignment and stability of the elements.
Static disc | 2 | A disc that remains fixed to cover and maintain the stability of the structure.
Solar spin | 1 | A part that allows for the movement of the solar panel for proper orientation.
Solar disc | 1 | A disc that connects the solar rotator with an installed servo motor and joins it with the rest of the structure.

Next, the assembly of the demonstrator is shown:

Note: The aluminum tape is used on the leaves’ surface to optimise the water collection. The double sided tape is used on the back of the solar panel to stick it on the “solar spin” part.

The water level sensor is placed in some slots inside the “water container” part.

When placing the electronic components into the mechanical assembly, it is necessary to use additional wires to extend the connections of the LDRs and the solar panel.

78

79

80

81

82

83

### 5. 3. Assembly of the Wind Demonstrator

5. 3. 1. Electronic Assembly

We will start by performing the assembly of the Wind Demonstrator. To perform this complete assembly you will need the following material:

1 x 5V DC Motor | 1 x 100nF / 1uF Capacitor
Used to generate voltage with wind power. | Used to eliminate unwanted noise generated by the DC motor.

### 2 x 1 kΩ Resistors

### 6 x Dupont Cable

(Male-Male) 10 cm

Used in the voltage divider that allows reading the voltage generated by the DC motor.

Necessary for making connections between the different components on the breadboard.

84

2 x Mini Breadboard | Soldering iron
Component necessary to connect the microcontroller board to the different components. | Necessary if the motor doesn't have wires included

### 1 x ESP32 DEVKIT V1 (30 pins)

Responsible for executing the programming that controls the operation of the electronics.

The objective of the setup will be to measure the amount of voltage generated by the motor, which will be attached to a mechanical structure that will rotate due to wind power. To measure the voltage obtained from the movement of the blades of the Demonstrator using the ESP32, we need to assemble a voltage divider to reduce the maximum voltage level (5V) to one suitable for the ESP32 (which operates at

85
3.3V). This way, we will be able to determine how much voltage is being generated by the wind.
For this new setup, it will be necessary to create a circuit from scratch. We will begin by placing the ESP32 on two mini breadboards. The corresponding setup is shown below.

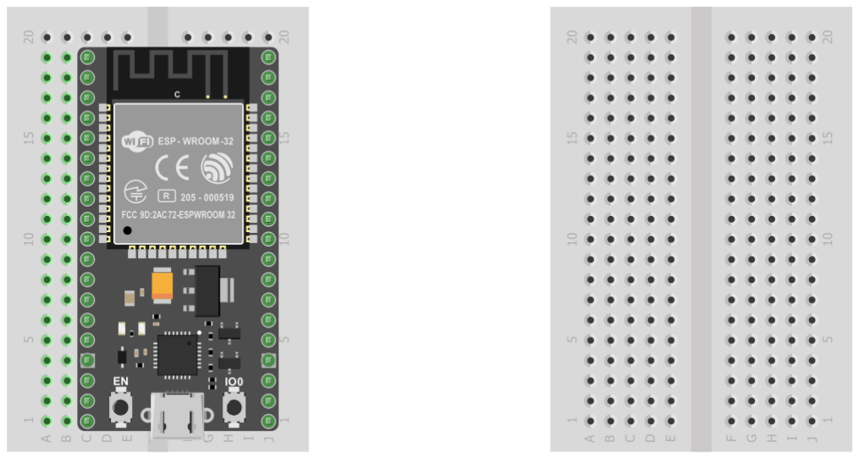
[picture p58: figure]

Next, a voltage divider will be assembled. The midpoint of this divider will be connected to pin VN. Additionally, a capacitor must be connected between the terminal of this pin and GND, which will act as a filter for unwanted variations in the measurement, as shown in the image below.

86

The final step in the electronic assembly of this demonstrator is to connect the motor to the previous setup. One of its terminals should be connected to GND, and the other terminal should be connected to the input of the voltage divider assembled earlier. The completed setup is presented below.

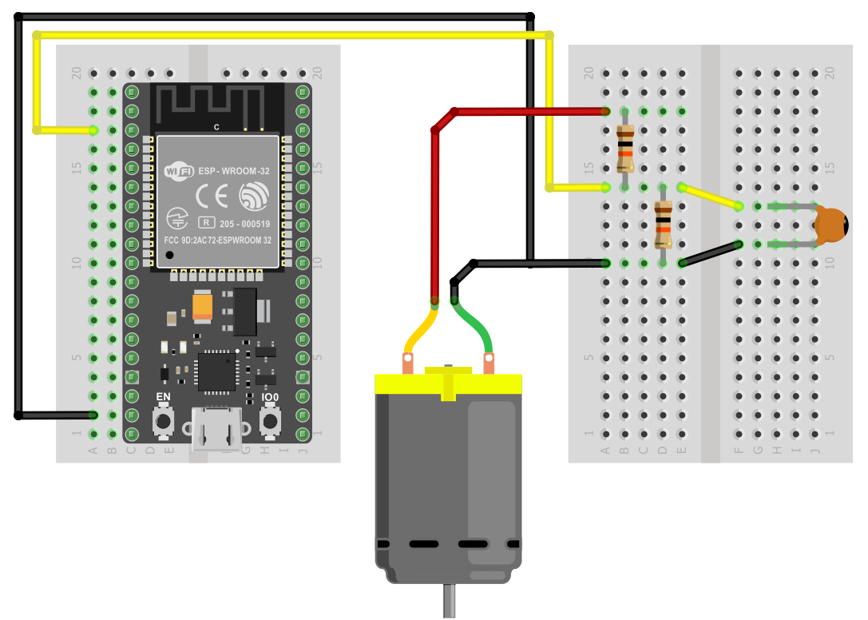
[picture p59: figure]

87
Let's check that the setup of this Demonstrator works correctly by using the following code snippet, where we only read the output of the voltage divider connected to the ESP32. By rotating the motor's rotor, we will see how the measurement gives different values through the Serial Monitor.

// Initialization block

void setup() {

// We initialize the Serial Monitor

Serial.begin(115200);

}

// Main loop of the code

void loop() {

// We take the measurement from the pin connected to the output of the voltage

//divider

int medicion = analogRead(39);

// We display the measurement on the Serial Monitor

Serial.println(medicion);

}
5. 3. 2. Mechanical Assembly

The components of this demonstrator are as follows:

Elemento | Cantidad | Descripción | Imagen
Base | 1 | It is the top section that secures the moving components, such as the blades and the motor shaft. It provides stability and allows the system to operate smoothly, facilitating the proper transfer of energy from the blades to the generator.
Drawer | 1 | It is the base that connects the different sections of the device, providing structural support and ensuring proper alignment between the motor, blades, and other essential components for

88
| | its operation.
Motor socket | 1 | This component will support and stabilize the motor, whose shaft will be connected to the bearing disc. This design will allow the connection of output pins, which will emit signals indicating the presence of movement.
Big L blade | 6 | It is a fixed blade that does not move. It is designed to be part of the static structure of the demonstrator, contributing to the overall stability and balance of the system.
Small L blade | 6 | It is a fixed blade that does not move, smaller than the previous piece. It is designed to be part of the static structure of the demonstrator, contributing to the overall stability and balance of the system.
Square blade | 8 | It is one of the key moving blades that rotates when driven by the wind. Its square design efficiently captures the wind's kinetic energy and converts it into rotational movement.
Big disc | 2 | It is a key component that serves as a structural support for the moving blades. This disk is designed to rotate when the blades capture the wind, transferring the rotational movement to the system's central shaft.

89
Small disc | 3 | It is a static component that does not move. Its main function is to act as part of the device's structural support, helping to maintain the proper alignment and stability of the moving elements, such as the blades and large disks.
Bearing disc | 1 | It is a crucial component used to reduce friction between the system's moving parts. This disk acts as a rotational support, allowing components like the Large Disk and the blades to spin smoothly and efficiently around the central shaft.
Top | 1 | It is a structural component placed at the top of the assembly, ensuring that all internal elements are protected and properly aligned.
Bearing | 1 | It is a mechanical component that allows rotating elements, such as the disks and blades, to move with minimal friction.
Wood joints | 3 | It is a structural component used to connect and secure the different wooden parts of the device.

The following shows how the demonstrator assembly is carried out:

Note: It is necessary to insert the 10-tooth gear onto the DC motor shaft before starting the assembly of the demonstrator.

90

91

92

93

94

95

## 6. DATA FROM THE SENSORS

### 6. 1. Serial Port

Communication through the serial port is one of the most commonly used methods for devices to connect with each other. It is also the primary means by which the ESP32 microcontroller, the ESP32, communicates with both the computer and other components. In a serial port, data is transmitted and received sequentially, sending bits one at a time through a single channel. In contrast, a parallel port transmits information simultaneously across multiple channels.

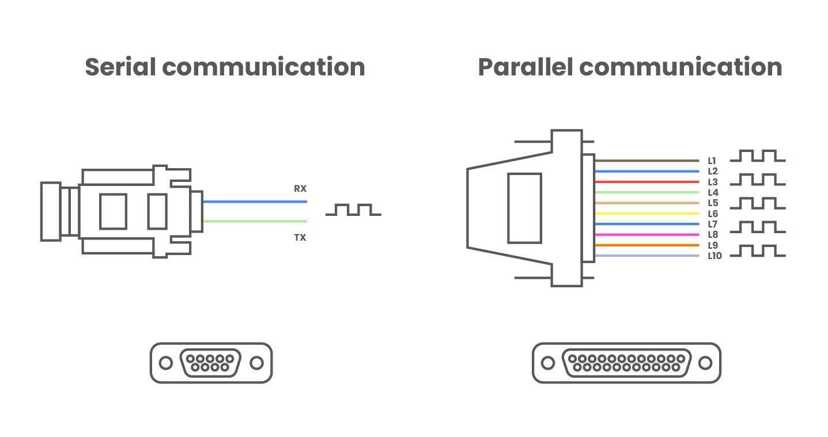
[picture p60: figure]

There are several types of serial ports, with the most popular being the USB (Universal Serial Bus) port. However, the older RS-232 serial port can also be found, as well as other serial communication protocols such as RS-485, I2C, SPI, among others. Serial communication is fundamental in microcontrollers, as all of them have at least one UART (Universal Asynchronous Receiver/Transmitter) unit. This type of serial port uses two channels: one for transmitting data (TX) and another for receiving it (RX).

96

The ESP32 board can communicate with the computer through a USB port, which is the same port used for programming it. This establishes a bidirectional communication channel that allows for both sending and receiving data. The tool that allows us to view the data sent from the ESP32 and, in turn, send information from the computer to the ESP32 is the Serial Monitor, which we have mentioned and used previously. This interface is integrated into the Arduino IDE and can be found in the upper right corner of the program, represented by the following icon:

97
Upon opening it, the Serial Monitor in the Arduino IDE appears as follows:

As you can see, the interface is quite simple and easy to use, with the following main elements:

- Sending Data: In the upper blank field, you can type and send data from the PC to the ESP32.
- Receiving Data: Most of the monitor is dedicated to displaying the data received from the ESP32.
- Autoscroll: Allows you to enable or disable automatic scrolling in the data reception window.
- Show Timestamp: Option to see the exact time each piece of data is received.
- Line Ending: Adds a type of line ending to the sent message.
- Baud Rate: Defines the transmission speed in baud (symbols per second). It is essential that the baud rate is the same for both the sender and the receiver for correct communication.

98

### 6. 2. Adafruit IO

Adafruit IO is an Internet of Things (IoT) platform that allows users to collect, visualize, and manage data from devices connected to the network. Offered by Adafruit, a company known for developing open-source hardware and software, Adafruit IO simplifies the connection and control of hardware projects like microcontrollers (Arduino, ESP32, Raspberry Pi, etc.) with the cloud.

To use this platform, we need to create a user account on its website. Once we have an account, we will click on the "IO" section at the top, next to Shop, Blog, and Forum. We will see the following window, and we should click on the icon with the yellow key:

When we click there, a window will open like the one in the following image, where we need to go to the "Arduino" section to obtain the data displayed there and modify

99
the same variables in the configuration code (config.h) of the Demonstrators mentioned earlier.

100
The next step is to create a Dashboard. To do this, we will click on the "Dashboards" menu at the top and then on the large blue button that says "New Dashboard." We will then see a pop-up window asking us to provide a name and a description for our new Dashboard. We can create one with any name we choose and add a description of what we will use it for.

Now we will proceed to enter the Dashboard we created, where we will see a nearly empty page. To add representations of the data that will arrive from our ESP32 in the Demonstrator, we need to click on the gear icon located in the upper right corner, which will open a menu where we will have the option to "Create New Block".

101

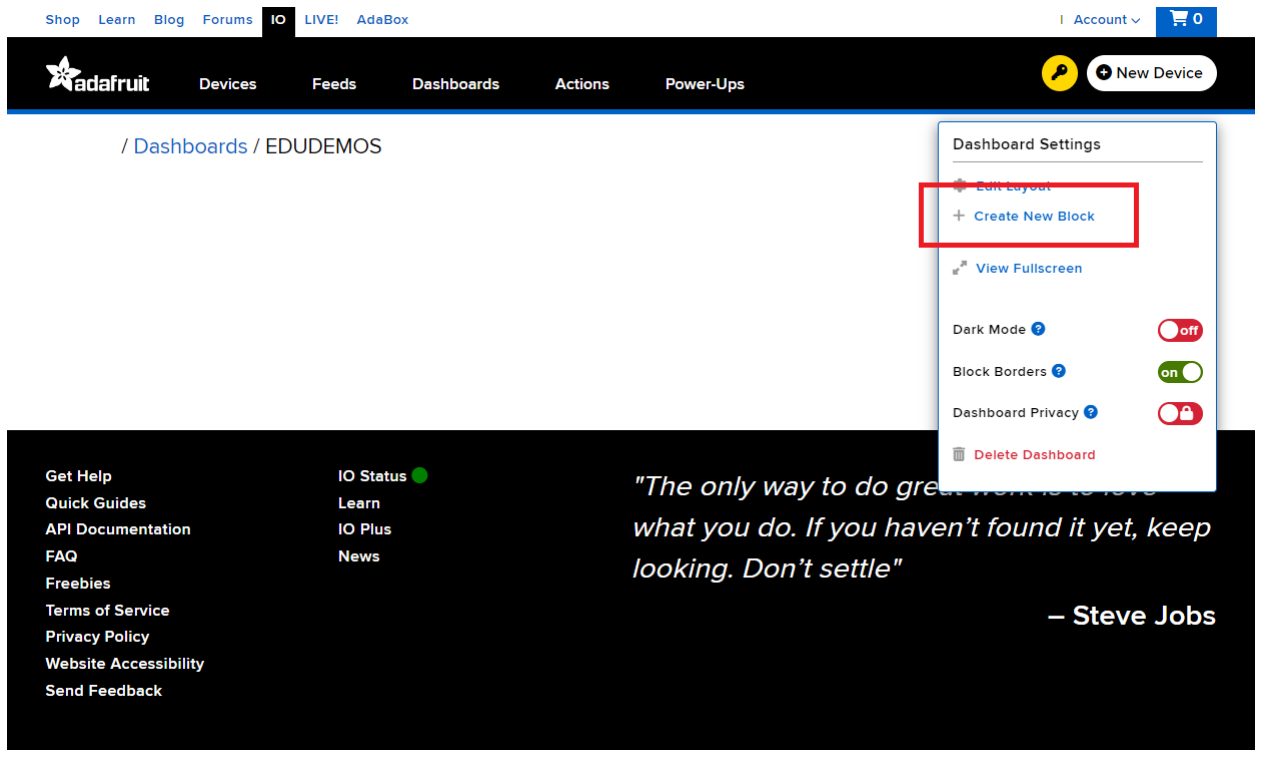
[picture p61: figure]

When we attempt to create a new block, a list of possible charts and indicators opens that can be included in our Dashboard. To represent the data in Adafruit IO, we need to create what they call Feeds, or data sources. These store the information sent or received from different devices connected to the platform. The Feeds we will need are: temperature, humidity, ldr, ldr1Feed, ldr2Feed, microvoltsMotor, microvoltsSolar, ledHighFeed, ledGoodFeed, and ledColdFeed.

We will use linear graphs, gauges, and indicators to represent the information received from the ESP32 of the ESP32 we are using as follows:

- Linear graph to represent Temperature in °C over time.
- Linear graph to represent Relative Humidity in % over time.
- Linear graph to represent the voltage generated by the DC Motor in µV over time.
- Linear graph to represent the voltage generated by the Solar Panel in µV over time.
- Gauge to represent the current Temperature in °C.
- Gauge to represent the current Relative Humidity in %.
- Gauge to represent the current voltage generated by the DC Motor in µV.

102
- Gauge to represent the current voltage generated by the Solar Panel in µV.
- Gauge to represent the current Average Light Intensity.
- Indicator to represent the status of the Cold LED.
- Indicator to represent the status of the Good LED.
- Indicator to represent the status of the Heat LED.

The goal will be to obtain a Dashboard at the end like the following:

103

## 7. OTA (Over-The-Air) UPDATES

OTA updates allow for the wireless updating of a device's firmware without the need to physically connect it to a computer. This is particularly useful in IoT devices, such as the ESP32, which are often located in remote or hard-to-access areas. With OTA updates, you can upload new code or improvements to the device without having to disassemble it or connect it via a USB cable.

To use OTA updates, we must first upload the complete code of the Demonstrators to our ESP32 board. Once uploaded and the connection to the Wi-Fi network and the Adafruit IO platform is established, we will be able to select an OTA port in the Arduino IDE (under Tools > Port) corresponding to the ESP32 we are using (it will have a name like "ESP32-OTA at" followed by the device's IP address on the Wi-Fi network).

104
Now, if you want to upload code via OTA updates, simply click the upload button. You will be prompted for a password (which is "admin" by default) and the program will then begin compiling. The first time you use OTA, the Operating System may request permission to carry out the task. Simply allow the application to run, and you will be able to upload code to your ESP32 board connected to the WiFi network without needing USB cables whenever you need.

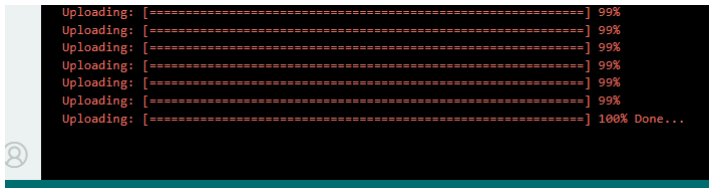
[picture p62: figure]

If at any point you need to change the name of the board when it is listed in the available ports or the password for performing the remote update, simply go to the source code of the Demonstrators and replace the values inside the parentheses and double quotes that you can see in the following lines (located within the setupOTA() function):

// Initialize ArduinoOTA for over-the-air updates

ArduinoOTA.setHostname("ESP32-OTA");

ArduinoOTA.setPassword("admin");

## 8. TYPICAL PROBLEMS

Problem | Verification | Solution
I can't upload the program to the ESP32 board. | Check that the USB cable is properly connected at both ends. | Disconnect and reconnect the cable properly at both ends.
| Check that the cable you're using is not only for charging. | Replace the cable with one that allows data transfer.
| Check that your computer's USB port is functioning correctly. | Change the USB port.

105

| Check that you have selected the correct COM port for the ESP32 board. | Select the COM port where the ESP32 is connected.
| Check that you have installed the necessary drivers (CP210X). | Install the drivers as indicated in section 3.1 Minimum Requirements.
I get an error when compiling the program. | Check if the error is related to a library. | Install the necessary libraries as indicated in section 3.2 Necessary Libraries.
| Check if the error is related to the syntax of the code. | Review the lines where you encounter the error and make corrections by comparing with the original code on GitHub.
The ESP32 doesn't connect to the WiFi network. | Check the credentials defined to connect to the WiFi. | Edit the WiFi network credentials (SSID and password) to the ones you want to use.
The ESP32 doesn't send data to Adafruit IO. | Check the credentials defined to connect to the platform. | Edit the platform credentials (Key and username) to the ones you want to use.
The ESP32 board doesn't turn on. | Check that it is connected by cable to an appropriate power source. | Connect the board to a USB port or another 5V power source.
The LEDs don't work properly. | Check that they are properly connected on the breadboard. | Connect each LED terminal in the correct place as indicated in the diagrams.
| Check that they are properly polarized. | Connect the longer terminal of the LED to the positive side and the shorter to the negative or GND.
| Check that the limiting resistor is properly connected. | Connect a resistor of at least 220 ohms in series with the LED.
The DHT sensor doesn't provide readings. | Check that it is properly powered. | Power the DHT with 3.3V on the positive terminal and GND on the negative.
| Check that the data terminal is connected to the same pin on the board as indicated in the program. | Connect the data terminal to the corresponding pin (D32)..
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

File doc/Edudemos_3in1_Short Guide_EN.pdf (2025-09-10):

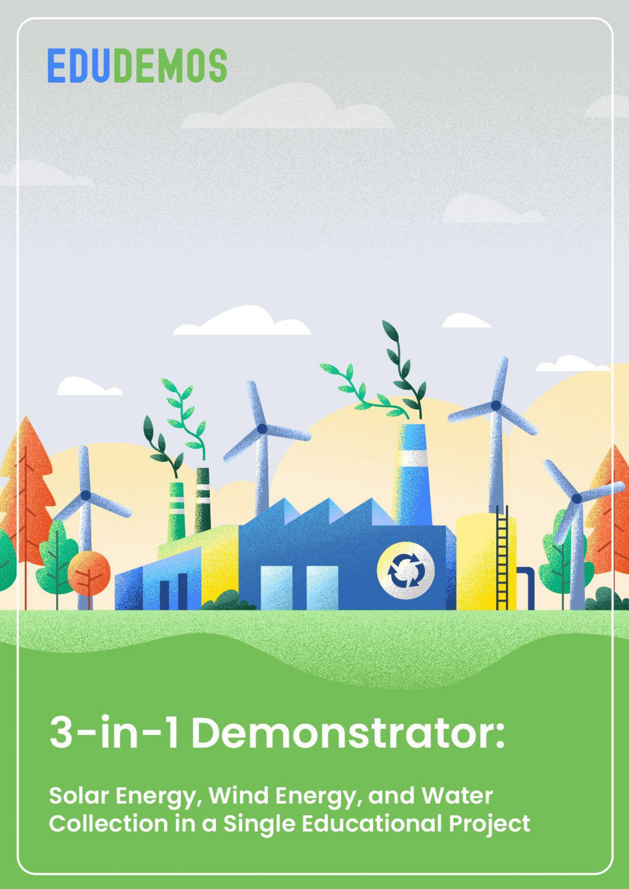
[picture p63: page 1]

# EDUDEMOS

# Funded by the European Union. Views and opinions expressed are however those of the author(s) only and do not necessarily reflect those of the European Union or the European Education and Culture Executive Agency (EACEA). Neither the European Union nor EACEA can be held

responsible for them.

EduDemoS 3in1 © 2025 by Gerda Stetter Stiftung – Technik macht Spaß!,

# Sergio Alonso Fundation, FINNOVA REGIO, GBS St. Gallen e IES El Rincón is licensed under

# Creative Commons Attribution-NonCommercial-ShareAlike 4.0 International. To view a copy of this license, visit https://creativecommons.org/licenses/by-nc-sa/4.0/

1

Funded by the European Union. Views and opinions expressed are however those of the author(s) only and do not necessarily reflect those of the European Union or the European Education and Culture Executive Agency (EACEA). Neither the European Union nor EACEA can be held responsible for them.

# 1. ASSEMBLY OF THE 3-IN-1 DEMONSTRATOR

The assembly of the 3x1 Demonstrator will be carried out modularly, addressing each section separately in the corresponding sections of this guide. This approach aims to simplify the process and enhance understanding, ensuring that the assembly is clear and accessible for those undertaking it. Each step is designed to guarantee a functional and effective outcome, even for individuals with no prior

experience in assembling demonstrators.

One of the main goals of this project is to promote the autonomy of educational institutions, enabling them to create their own demonstrators if they have 3D printers on-site. For this reason, we have made the necessary printing files available for the fabrication of the components, which can be downloaded via the following

link: 3D Printing Files. (https://drive.google.com/drive/folders/1F19XPgi768G87Ds_K66nvXBx-3E4KJT6) With this tool, we aim to empower educational institutions to independently and efficiently integrate these demonstrators into their activities.

# 1.1. List of Materials

- 1 x ESP32 DEVKIT V1 with 30 pins - 2 x Mini breadboards with 170 tie-points - 1 x DHT11 module, maximum width 14 mm, with or without built-in LED - 10/12* x Male-to-male jumper wires, 10 cm - 5 x Male-to-male jumper wires, 20 cm - 3 x Male-to-female jumper wires, 10 cm - 10 x Male-to-female jumper wires, 20 cm - 5 x 1k ohm resistors - 1 x Capacitor, 100nF or 1uF - 3 x Colored LEDs (preferably Red, Green, and Blue) - 1 x Solar panel, maximum dimensions: 45 mm x 60 mm - 1 x Water level sensor, 6 cm x 2 cm - 1 x 5V DC motor, maximum dimensions: 28 mm diameter and 45 mm length - 1 x SG-90 Servo motor - 1 x Voltage detector - 2 x Photoresistors standalone GL5528

2

- 1 x 6203 bearing, either ZZ or 2RS type: 40 mm outer diameter, 17 mm inner diameter, and 12 mm height - 3 x Wooden dowels: 8 mm diameter and 40 mm length - 1 x Motor gear: 2 mm inner diameter, 10 teeth, and 5 mm height - 1 x Data transfer cable USB to microUSB - 1 x Aluminum tape, 5 cm wide - 1 x Double sided tape, 3 cm de wide

# * If the Motor DC doesn’t come with wires, you will need 12 male-to-male jump wires

of 10 cm.

# Tools you might need:

- Soldering iron: if the Motor DC or the Solar Panel don’t come with wires.
- Flat head screw driver 2 mm: for the voltaje sensor.

3

# 1. 2. Assembly of the Water and Solar Demonstrator

# 1. 2. 1. Electronic Assembly (Water Component)

# We will begin by assembling the water collector. To complete this assembly, you will need the following materials:


1 x DHT-11 Sensor | 3 x 1 kΩ Resistors
Responsible for measuring ambient temperature and humidity. | Used to limit the current flowing through LED diodes.

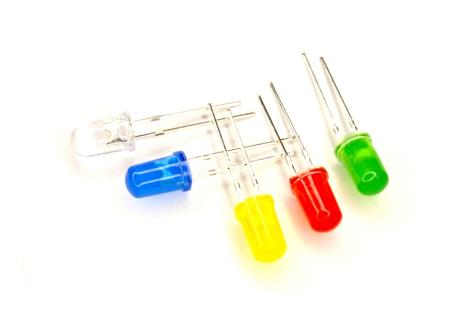
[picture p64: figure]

3 x Colored LEDs (Preferably Red,

# Green, and Blue)

# 1 x Dupont Cables (Male-Male) 10cm

# Used as visual indicators of the

measured temperature range.

# Necessary for making connections between the different components on

the breadboard.

4

# 2 x Mini Breadboard

# 6 x Dupont Cables (Male-Female) 20cm

# Component necessary to connect the microcontroller board to the different

components.

# Necessary for making connections between the different components on

the breadboard.

1 x Water level sensor | 1 x ESP32 DEVKIT V1 (30 pins)
Used to measure the water level in the tank. | Responsible for executing the programming that controls the operation of the electronics.

# The objective of the assembly is to obtain the values of ambient temperature and humidity, and based on the temperature value, to light up a specific LED as indicators

of danger for high or low temperatures. In this way, if the temperature is below 20ºC, the Blue LED will light up; if it is above 25ºC, the Red LED will light up; and if it is between those values (between 20 and 25ºC), the Green LED will light up.

5

# The first step is to place the ESP32 board on two small breadboards to have enough space to connect the components we will need later. Below, you can see the result:


# Once we have the microcontroller placed on the two breadboards, we will start connecting the colored LEDs with their current-limiting resistors. We will begin by

placing the Blue LED and one of the 1 kΩ resistors in series. We will connect the positive of the LED to pin D5 and use any GND pin to connect the negative of the circuit. Below, you can see the indicated assembly.

Note: The LED diode indicates the polarity of the connection at a glance by the length of its leads. The longer lead corresponds to the anode, or positive, and the shorter one is the cathode, or negative. In the diagram, the longer lead is the one connected in series with the resistor.

6

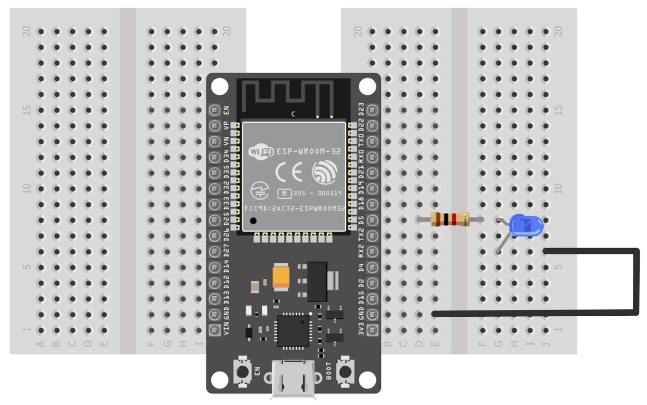
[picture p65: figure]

# To verify the correct functioning of the assembly, we can upload the following code to the ESP32:

#define ledPin1Cold 5 // Define the pin where the Blue LED is connected

// Initialization block

void setup() {

// We configure the operating mode of the LED pin as an output

pinMode(ledPin1Cold, OUTPUT);

}

// Main loop of the code

void loop() {

digitalWrite(ledPin1Cold, LOW); // We turn off the LED

delay(1000); // We wait 1 second = 1000 milliseconds

digitalWrite(ledPin1Cold, HIGH); // We turn on the LED

delay(1000); // We wait 1 second

}

7

# This small program makes the Blue LED blink, changing its state between on and off every second. If it does not work correctly, check that the LED is oriented properly (remember that the longer lead is the positive terminal, while the shorter one is the

negative) and connected appropriately with the current-limiting resistor.

# The next step in the assembly will be to add a second LED. This time, we will place and connect the Green LED to pin D18 with its resistor. You can see the indicated assembly

schematic in the following image.


# Let's verify that the assembly is correct again. We will use the code below to check

that the new LED is also properly placed.

8

#define ledPin1Cold 5 // Define the pin where the Blue LED is connected

#define ledPin2Good 18 // Define the pin where the Green LED is connected

// Initialization block

void setup() {

// We configure the operating mode of the LEDs pins as outputs

pinMode(ledPin1Cold, OUTPUT);

pinMode(ledPin2Good, OUTPUT);

}

// Main loop of the code

void loop() {

digitalWrite(ledPin1Cold, LOW); // We turn off the Blue LED

digitalWrite(ledPin2Good, LOW); // We turn off the Green LED

delay(1000); // We wait 1 second = 1000 milliseconds

digitalWrite(ledPin1Cold, HIGH); // We turn on the Blue LED

digitalWrite(ledPin2Good, HIGH); // We turn on the Green LED

delay(1000); // We wait 1 second

}

# As you can see, the objective of the code remains the same: to turn both LEDs on and off, changing their state every second. If the Blue and Green LEDs are changing states

correctly, we can consider the current assembly valid and proceed to the next step.

# To complete the assembly of the colored LEDs needed to fulfill the established objective for this part of the Demonstrator, we need to connect the last LED, which is Red, to pin D19. Proceed to assemble the LED diode and the corresponding last

resistor, as shown in the following image.

9

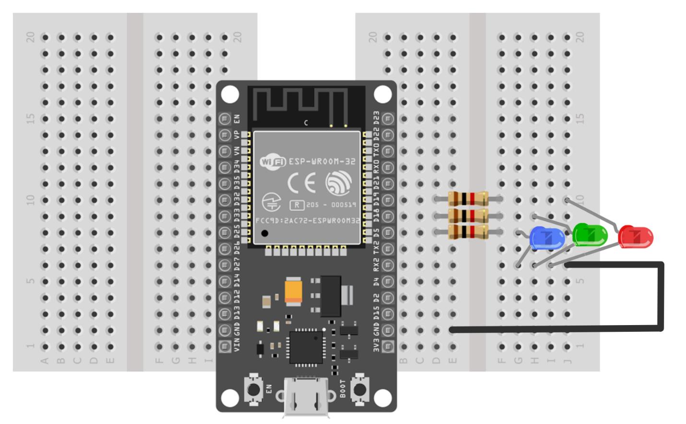
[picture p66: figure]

# We will check that it is correct by using the same programming as in the previous cases, generating a blink in all three colored LEDs. The code for this is as follows:

#define ledPin1Cold 5 // Define the pin where the Blue LED is connected

#define ledPin2Good 18 // Define the pin where the Green LED is connected

#define ledPin3Heat 19 // Define the pin where the Red LED is connected

// Initialization block

void setup() {

// We configure the operating mode of the LEDs pins as outputs

pinMode(ledPin1Cold, OUTPUT);

pinMode(ledPin2Good, OUTPUT);

pinMode(ledPin3Heat, OUTPUT);

}

// Main loop of the code

void loop() {

digitalWrite(ledPin1Cold, LOW); // We turn off the Blue LED

digitalWrite(ledPin2Good, LOW); // We turn off the Green LED

digitalWrite(ledPin3Heat, LOW); // We turn off the Red LED

10

delay(1000); // We wait 1 second = 1000 milliseconds

digitalWrite(ledPin1Cold, HIGH); // We turn on the Blue LED

digitalWrite(ledPin2Good, HIGH); // We turn on the Green LED

digitalWrite(ledPin3Heat, HIGH); // We turn on the Red LED

delay(1000); // We wait 1 second

}

# The next step is to add and connect the DHT11 sensor to pin D32, either as an individual component or on a module. Below is the assembly completed so far along with the

connections for the DHT11 sensor.

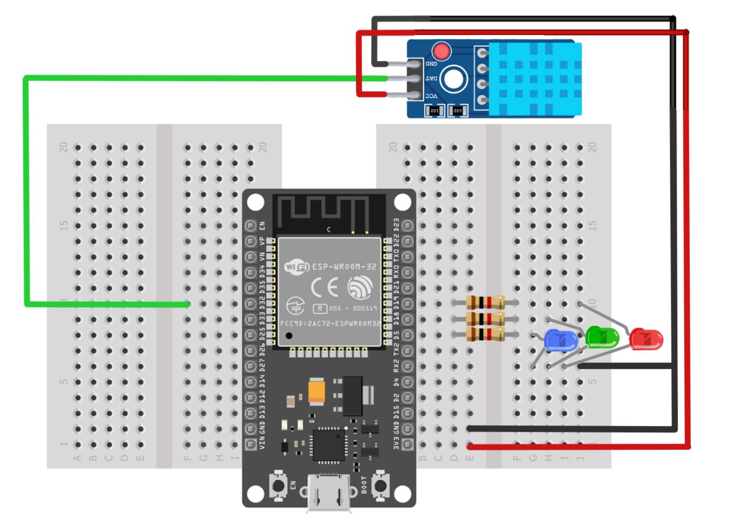
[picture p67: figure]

Note: Make sure that the GND and VCC connections of the DHT11 sensor match the actual pinout of the component, as they may differ from what is shown in the diagram.

11

# We will now check the correct functioning of the DHT-11 sensor. Below is a test code

for the entire assembly completed for this part of the project. Upload the program,

# and you will see that, in addition to the colored LEDs blinking as they have done so far, the ESP32 board will send the obtained measurements of ambient temperature (in °C) and relative humidity (in %) to the Serial Monitor every couple of seconds (you

can see the button to open it in the following image).

#include <DHT.h> // We include the necessary library to control DHT.

#define ledPin1Cold 5 // Define the pin where the Blue LED is connected

#define ledPin2Good 18 // Define the pin where the Green LED is connected

#define ledPin3Heat 19 // Define the pin where the Red LED is connected

#define DHTPIN 32 // Define the pin to which the DHT is connected

#define DHTTYPE DHT11 // Define the type of DHT sensor to use

// Define the type of DHT sensor to be usedCreate an object of type DHT with the corresponding

configuration

DHT myDHT11(DHTPIN, DHTTYPE);

// Initialization block

void setup() {

// We configure the operating mode of the LEDs pins as outputs

pinMode(ledPin1Cold, OUTPUT);

pinMode(ledPin2Good, OUTPUT);

pinMode(ledPin3Heat, OUTPUT);

// Initialize the Serial monitor

Serial.begin(115200);

12

// Initialize the DHT sensor

myDHT11.begin();

}

// Main loop of the code

void loop() {

digitalWrite(ledPin1Cold, LOW); // We turn off the Blue LED

digitalWrite(ledPin2Good, LOW); // We turn off the Green LED

digitalWrite(ledPin3Heat, LOW); // We turn off the Red LED

delay(1000); // We wait 1 second = 1000 milliseconds

digitalWrite(ledPin1Cold, HIGH); // We turn on the Blue LED

digitalWrite(ledPin2Good, HIGH); // We turn on the Green LED

digitalWrite(ledPin3Heat, HIGH); // We turn on the Red LED

delay(1000); // We wait 1 second

// We obtain the DHT sensor measurements

float temperature = myDHT11.readTemperature();

float humidity = myDHT11.readHumidity();

// We show the values per monitor Serial

Serial.print("Temperature: ");

Serial.println(temperature);

Serial.print("Humidity: ");

Serial.println(humidity);

}

# With the monitor open, make sure that the dropdown located furthest to the right on the Monitor is set to "115200". Now you will be able to see the data sent by the ESP32 from the DHT-11 constantly and verify that the assembly up to this point is functioning

correctly.

# The next component to be added is the water level sensor module. Connect the sensor to pin VN. In the following image you can see how the assembly will look like:

13

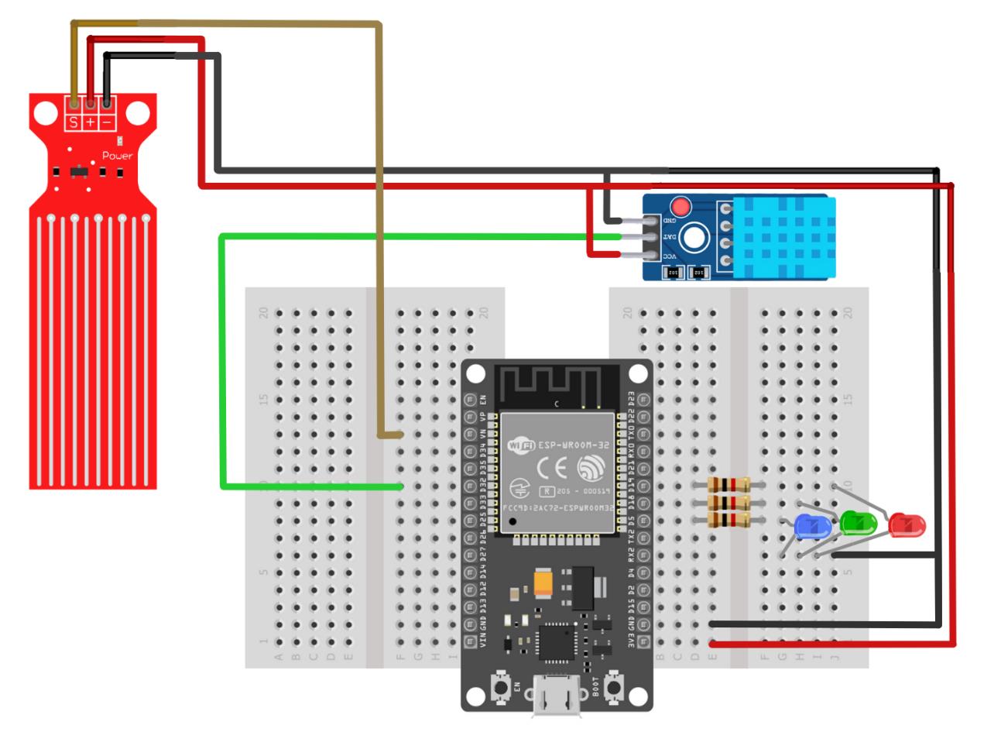
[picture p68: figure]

# Now we are going to verify the operation of the water level sensor by constantly reading and displaying the measured value of the sensor on the serial monitor:

//Water sensor calibration

const int WaterSensorPin = 39; // Analog Value from VN PIN

void setup() {

Serial.begin(115200);

}

void loop() {

int sensorValue; // Variable to store sensor values

sensorValue = analogRead(WaterSensorPin); // Read the value from the sensor

Serial.println(sensorValue); // Print value in serial monitor

delay(100);

}

14

15

# 5. 2. 2. Electronic Assembly (Solar Component)

# We will begin by assembling the solar component. To complete this assembly, you will need the following materials:

1 x SG-90 Servo Motor | 2 x Photoresistors -
Used to move the solar demonstrator and orient it toward sunlight. | Used to measure the level of received light intensity.
2 x 1 kΩ Resistors | 9 x Dupont Cable (Male-Male) 10 cm
Used only with the independent LDRs to assemble a voltage divider controlled by light intensity. | Necessary for making connections between the different components on the breadboard.

16

# 5 x Dupont cable (Male-Male) 20cm

# 3 x Dupont cable (Male-Female) 10cm

# Necessary for making connections between the different components on

the breadboard.

# Necessary for making connections between the different components on

the breadboard.

# 4 x Dupont cable

(Male-Female) 20cm | 1 x Voltage sensor
Necessary for making connections between the different components on the breadboard. | Used alongside the solar panel to detect sunlight.

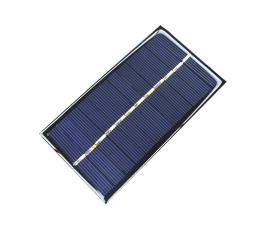
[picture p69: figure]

# 1 x Solar Panel

Used to detect sunlight.

17

# The objective of the assembly will be to determine the orientation of the incidence of sunlight with the LDRs and rotate the Demonstrator to maximize the amount of

sunlight hitting the panel.

# The assembly of the solar component will begin from the last assembly seen in the

previous section. In this assembly, an LDR and a resistor will be added in series,

# forming a voltage divider controlled by light intensity. To obtain the value from the sensor, the digital output will be connected to pin D34 of the ESP32. The assembly can be seen below:


# To check the functionality of the new elements added to the assembly, we will use a code that only reads the LDR value to light up the Red LED with greater or lesser intensity based on the brightness measured by the photoresistor. You can see the code to upload below:

18

#define ldrPin1 34 // Define the pin to which the LDR is connected

// Initialization block

void setup() {

// Initialize the serial monitor

Serial.begin(115200);

}

// Main loop of the code

void loop() {

// We take the reading of the pin where the LDR is located.

int reading_ldr_1 = analogRead(ldrPin1);

// Display the value on the Serial monitor

Serial.print("Luminosity 1: ");

Serial.println(reading_ldr_1);

}

# Next, the second LDR with its resistor should be added. To obtain the reading value from this sensor, the digital output will be used, as in the previous case, but this one will be connected to pin D35. Below, you can see the assembly with both LDRs for the

current part of the Demonstrator.

19

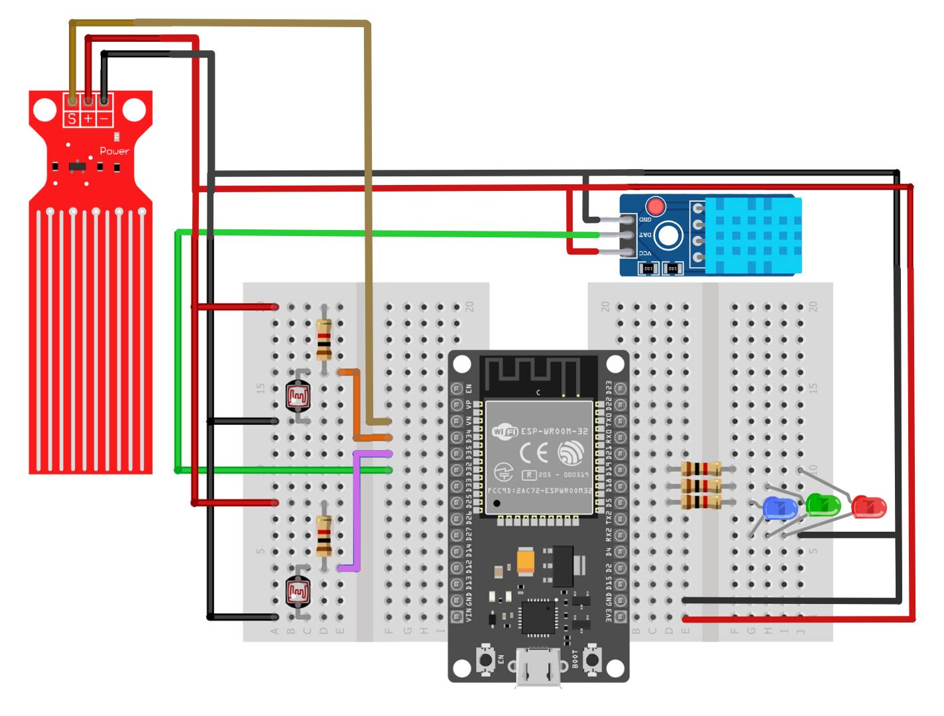
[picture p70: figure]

Let's verify that the connections have been made correctly using the following code,

# which is very similar to the previous one but displays the measurement values from

both photoresistors.

#define ldrPin1 34 // Define the pin to which the first LDR is connected

#define ldrPin2 35 // Define the pin to which the second LDR is connected

// Initialization block

void setup() {

// Initialize the serial monitor

Serial.begin(115200);

}

// Main loop of the code

void loop() {

// We take the readings of the pins where the LDRs are located

20

int reading_ldr_1 = analogRead(ldrPin1);

int reading_ldr_2 = analogRead(ldrPin2);

// We display the first value on the Serial monitor

Serial.print("Luminosity 1: ");

Serial.println(reading_ldr_1);

// We display the second value on the Serial monitor

Serial.print("Luminosity 2: ");

Serial.println(reading_ldr_2);

}

# The next component to be added to the assembly is a servo motor. This will be connected to both power rails (the red wire to the positive and the black wire to the negative), and the yellow wire (which is the control signal) will be connected to pin

D25.

# We will check the operation of the servo motor by uploading the following code to the ESP32, which sweeps the servo between the positions of 0º, 90º, and 180º in a loop

repeatedly.

21

#include <ESP32Servo.h> // Include the necessary library to control the servomotor

#define servoPin 25 // Define the pin where the servomotor is connected

// We create an object of type Servo to control it

Servo myServo;

// Initialization block

void setup() {

// We associate the servo we created to the pin where it is connected

myServo.attach(servoPin);

// We place the servo in an initial position of 0º

myServo.write(0);

}

// Main loop of the code

void loop() {

myServo.write(0); // We move the servomotor to 0º

delay(1000); // We wait 1 second = 1000 milliseconds

myServo.write(90); // We move the servomotor to 90º

delay(1000); // We wait 1 second

myServo.write(180); // We move the servomotor to 180º

delay(1000); // We wait 1 second

}
Note: Attach the helix to the servo. Screws are not needed to secure it.

# The last component we will connect to the ESP32 will be a voltage detector. This module should be powered through both power rails (Vcc and GND). The signal line

will be connected to pin VP.

22

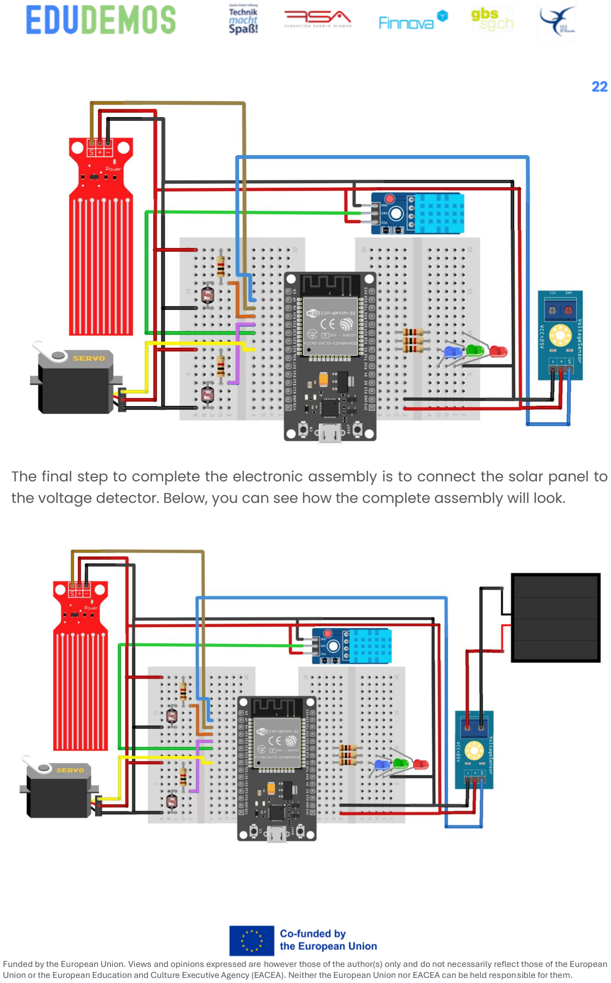
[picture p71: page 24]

# The final step to complete the electronic assembly is to connect the solar panel to

the voltage detector. Below, you can see how the complete assembly will look.

23

# We will check the functionality of the complete solar detector by using the following code, which simply reads the signal from the voltage detector module and turns on

the Blue LED if it detects voltage.

#define ledPin1Cold 5 // Define the pin where the Blue LED is connected

#define detectorPin 36 // Define the pin where the Voltage Detector is connected

// Initialization block

void setup() {

// We configure the operating mode of the LED pin as an output

pinMode(ledPin1Cold, OUTPUT);

}

// Main loop of the code

void loop() {

// We take the reading of the Detector Module

bool tension_detectada = digitalRead(detectorPin);

// We check if there is tension or not

if(tension_detectada) { // Yes, there is tension

digitalWrite(ledPin1Cold, HIGH); // We turn on the Blue LED

} else { // No tension

digitalWrite(ledPin1Cold, LOW); // We turn off the Blue LED

}

}

# Below is a test code to verify that all the sensors are getting readings and working correctly:

//include the necessary libraries #include <ESP32Servo.h>

#include "DHT.h"

// Pin definitions and constants

#define ldrPin1 34 // set ldr 1 Analog input pin of East ldr as an integer

#define ldrPin2 35 // set ldr 2 Analog input pin of West ldr as an integer

24

#define DHTPIN 32

#define DHTTYPE DHT11

#define ledPin1Cold 5

#define ledPin2Good 18

#define ledPin3Heat 19

#define SolarPin 36

// Global variables

DHT dht(DHTPIN, DHTTYPE);

Servo myservo;

int valldr1 = 0 ;

int valldr2 = 0 ;

int averageLdrValue = 0;

int servopos = 90; // initial position of the Horizontal movement controlling servo

motor

int tolerance = 20; // allowable tolerance setting - so solar servo motor isn't

constantly in motion

float lastMicrovolts = 0;

const int WaterSensorPin = 39; // Analog Value from VN PIN

int sensorValue; // Variable to store sensor values

void setup(){

Serial.begin(115200);

analogReadResolution(12); // ESP32 has a 12-bit ADC

analogSetAttenuation(ADC_11db); // Set attenuation for higher sensitivity

pinMode(4, INPUT);

dht.begin(); // Start the DHT sensor

pinMode(ledPin1Cold, OUTPUT);

pinMode(ledPin2Good, OUTPUT);

pinMode(ledPin3Heat, OUTPUT);

myservo.attach(25); // attaches the servo on digital pin 2 to the horizontal movement

servo motor

pinMode(ldrPin1, INPUT); //set East ldr pin as an input

pinMode(ldrPin2, INPUT); //set West ldr pin as an input

myservo.write(servopos); // write the starting position of the horizontal movement

servo motor

delay(1000); // 1 second delay to allow the solar panel to move to its staring position

before commencing solar tracking

}

25

void loop(){

Serial.println("----------------------------- Measured Solar (V) ------------------

---------- ");

int solarVoltagedV = analogRead ( SolarPin); //dV

int solarVoltage = solarVoltagedV * 10;

Serial.print("Voltage of Solar Panel: ");

Serial.println(solarVoltage);

// Calculate voltage

float voltage = (solarVoltage / 4095.0) * 3.3; // For 12-bit ADC (0-4095)

Serial.print("Measured voltage (V): ");

Serial.println(voltage); // Display the measured voltage

// Convert to microvolts

float microvoltsSolar = voltage * 1000000.0;

Serial.print("Input voltage (µV): ");

Serial.println(microvoltsSolar);

// Apply a minimum threshold to filter noise

const float threshold = 10.0; // Threshold in microvolts

if (microvoltsSolar < threshold) {

microvoltsSolar = 0;

}

// Check if the microvolts value has changed

if (microvoltsSolar != lastMicrovolts) {

Serial.print("Send voltage: ");

Serial.print(microvoltsSolar, 2); // Display with 2 decimal places

Serial.println(" µV");

// Update the last microvolts value

lastMicrovolts = microvoltsSolar;

}

Serial.println("----------------------- Measured Temperature / Humidity -----------

------------ ");

// Read values from DHT sensor

float h = dht.readHumidity();

float t = dht.readTemperature();

// Check if readings are valid

if (isnan(h) || isnan(t)) {

26

Serial.println("Failed to read from DHT sensor!");

return;

}

// Print sensor values

Serial.print("Temperature: ");

Serial.print(t);

Serial.print(" °C, Humidity: ");

Serial.print(h);

Serial.print(" %");

// Example LED control based on temperature

if (t < 20) {

digitalWrite(ledPin1Cold, HIGH);

digitalWrite(ledPin2Good, LOW);

digitalWrite(ledPin3Heat, LOW);

Serial.println("Cold is HIGH");

} else if (t >= 20 && t < 25) {

digitalWrite(ledPin1Cold, LOW);

digitalWrite(ledPin2Good, HIGH);

digitalWrite(ledPin3Heat, LOW);

Serial.println("Good is HIGH");

} else {

digitalWrite(ledPin1Cold, LOW);

digitalWrite(ledPin2Good, LOW);

digitalWrite(ledPin3Heat, HIGH);

Serial.println("Heat is HIGH");

}

Serial.println("----------------------------- Measured Water Level ----------------

------------- ");

int sensorValue; // Variable to store sensor values

sensorValue = analogRead(WaterSensorPin); // Read the value from the soil moisture

sensor

//Check watersensor calibration first

if (sensorValue >= 2000) { //These value represents de max value given

sensorValue = 1980; //This value would return a 99% value

}

float waterlevel = (sensorValue*100)/2000 ; //Calculation to return the %

Serial.print("Water level: "); // Print value in serial monitor

Serial.print(waterlevel); // Print value in serial monitor

Serial.println(" %"); // Print value in serial monitor

27

Serial.println("----------------------------- Measured LDR and Servo --------------

--------------- ");

// Read LDR values

valldr1 = analogRead(ldrPin1); // read the value of ldr 1

valldr2 = analogRead(ldrPin2); // read the value of ldr 2

// Invert readings so low values mean darkness and high values mean light

averageLdrValue = (valldr1 + valldr2) / 2;

// Print readings for debugging

Serial.print("LDR 1: ");

Serial.print(valldr1);

Serial.print(" | LDR 2: ");

Serial.println(valldr2);

Serial.print("Average LDR: ");

Serial.println(averageLdrValue);

if((abs(valldr1 - valldr2) <= tolerance) || (abs(valldr2 - valldr1) <= tolerance)) {

//no servo motor horizontal movement will take place if the ldr value is within the

allowable tolerance

}else {

if(valldr1 > valldr2) // if ldr1 senses more light than ldr2

{

servopos = servopos+10; // decrement the 90 degree position of the horizontal servo

motor - this will move the panel position Eastward

}

if(valldr1 < valldr2) // if ldr2 senses more light than ldr1

{

servopos = servopos-10; // increment the 90 degree position of the horizontal motor -

this will move the panel position Westward

}

}

if(servopos > 180) {servopos = 180;} // reset the horizontal position of the motor to

180 if it tries to move past this point

if(servopos < 0) {servopos = 0;} // reset the horizontal position of the motor to 0 if

it tries to move past this point

myservo.write(servopos); // write the starting position to the horizontal motor

// Print the servo angle

Serial.print("Servo angle: ");

Serial.print(servopos);

delay(5000);

28

}

# 1. 2. 3. Mechanical Assembly of the Water and Solar Demonstrator

# The elements that make up this demonstrator are as follows:

Element | Quantify | Description | Image
Base | 1 | It is the upper part that secures the moving components, such as the blades and the motor shaft. It provides stability and allows the system to operate smoothly, facilitating the correct transfer of energy from the blades to the generator.

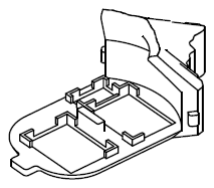
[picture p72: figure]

Drawer | 1 | It is the base that connects the different sections of the device, providing structural support and ensuring proper alignment between the motor, the blades, and other essential components for its operation.
Water container | 1 | This part is capable of storing the water that falls into it.
Leaf | 8 | A sheet that allows liquids to enter the water collection container.

29
Small disc | 3 | It is a static component that does not move. Its primary function is to act as part of the structural support of the device, helping to maintain proper alignment and stability of the elements.
Static disc | 2 | A disc that remains fixed to cover and maintain the stability of the structure.
Solar spin | 1 | A part that allows for the movement of the solar panel for proper orientation.
Solar disc | 1 | A disc that connects the solar rotator with an installed servo motor and joins it with the rest of the structure.

# Next, the assembly of the demonstrator is shown:

Note: The aluminum tape is used on the leaves’ surface to optimise the water collection. The double sided tape is used on the back of the solar panel to stick it on the “solar spin” part.

The water level sensor is placed in some slots inside the “water container” part.

When placing the electronic components into the mechanical assembly, it is necessary to use additional wires to extend the connections of the LDRs and the solar panel.

30

31

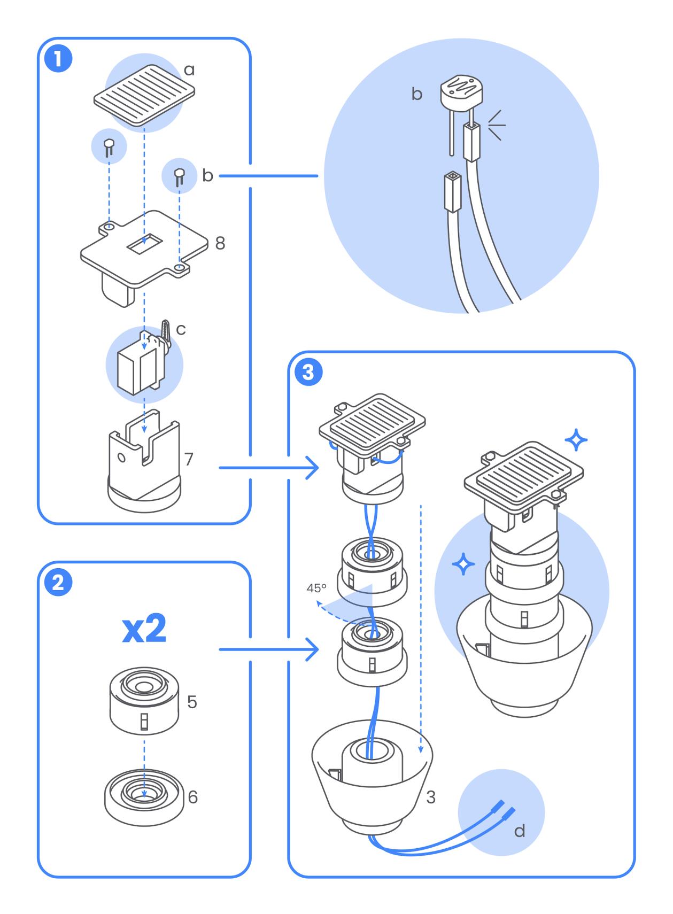
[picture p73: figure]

32

33

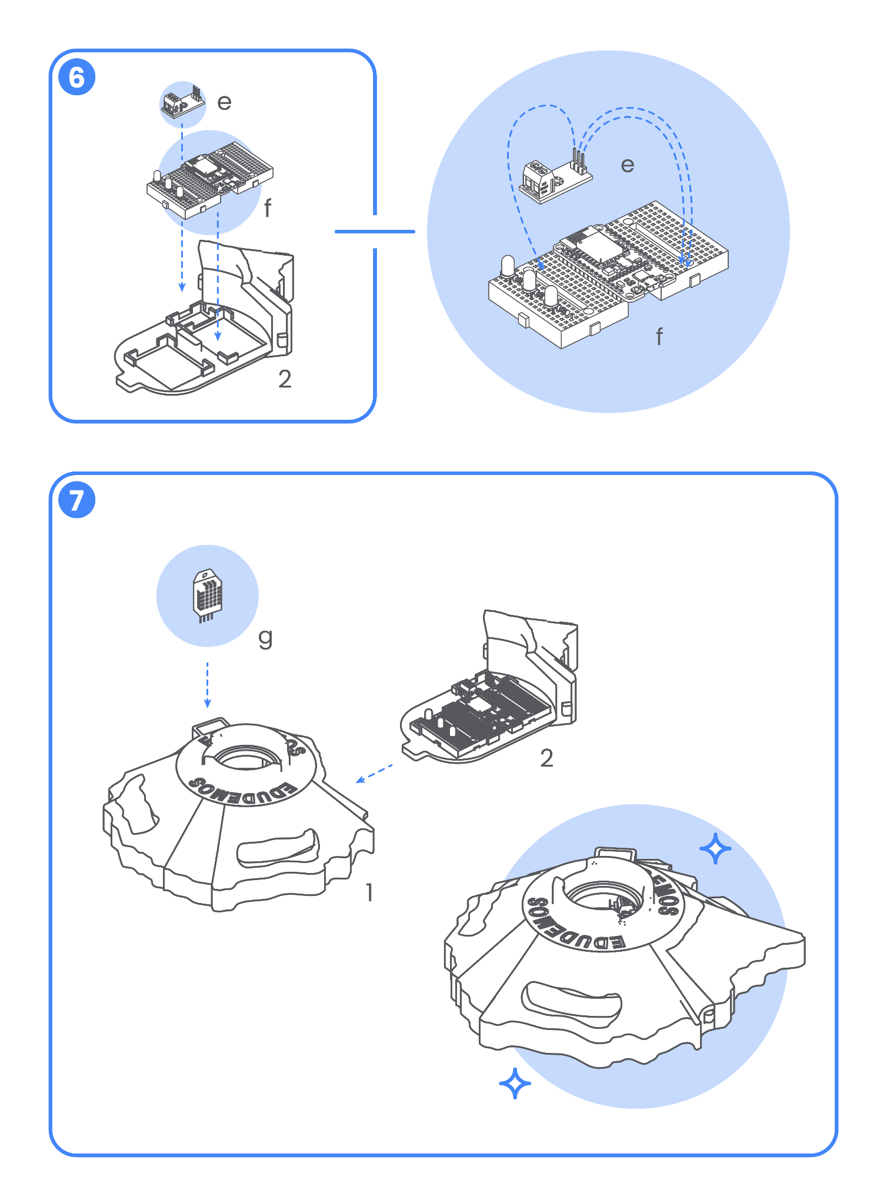
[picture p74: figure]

34

35

# 1. 3. Assembly of the Wind Demonstrator

# 1. 3. 1. Electronic Assembly

# We will start by performing the assembly of the Wind Demonstrator. To perform this complete assembly you will need the following material:

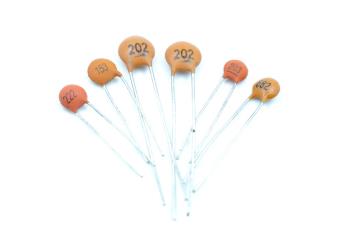
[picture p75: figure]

1 x 5V DC Motor | 1 x 100nF / 1uF Capacitor
Used to generate voltage with wind power. | Used to eliminate unwanted noise generated by the DC motor.

# 2 x 1 kΩ Resistors

# 6 x Dupont Cable (Male-Male) 10 cm

# Used in the voltage divider that allows reading the voltage generated by the

DC motor.

# Necessary for making connections between the different components on

the breadboard.

36

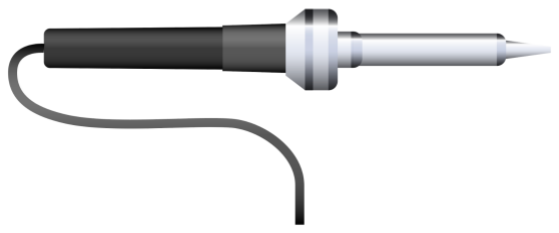
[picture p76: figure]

2 x Mini Breadboard | Soldering iron
Component necessary to connect the microcontroller board to the different components. | Necessary if the motor doesn't have wires included

# 1 x ESP32 DEVKIT V1 (30 pins)

# Responsible for executing the programming that controls the operation of the

electronics.

The objective of the setup will be to measure the amount of voltage generated by the motor, which will be attached to a mechanical structure that will rotate due to wind power. To measure the voltage obtained from the movement of the blades of the Demonstrator using the ESP32, we need to assemble a voltage divider to reduce the maximum voltage level (5V) to one suitable for the ESP32 (which operates at

37

# 3.3V). This way, we will be able to determine how much voltage is being generated

by the wind.

# For this new setup, it will be necessary to create a circuit from scratch. We will begin by placing the ESP32 on two mini breadboards. The corresponding setup is shown

below.


# Next, a voltage divider will be assembled. The midpoint of this divider will be connected to pin VN. Additionally, a capacitor must be connected between the terminal of this pin and GND, which will act as a filter for unwanted variations in the

measurement, as shown in the image below.

38

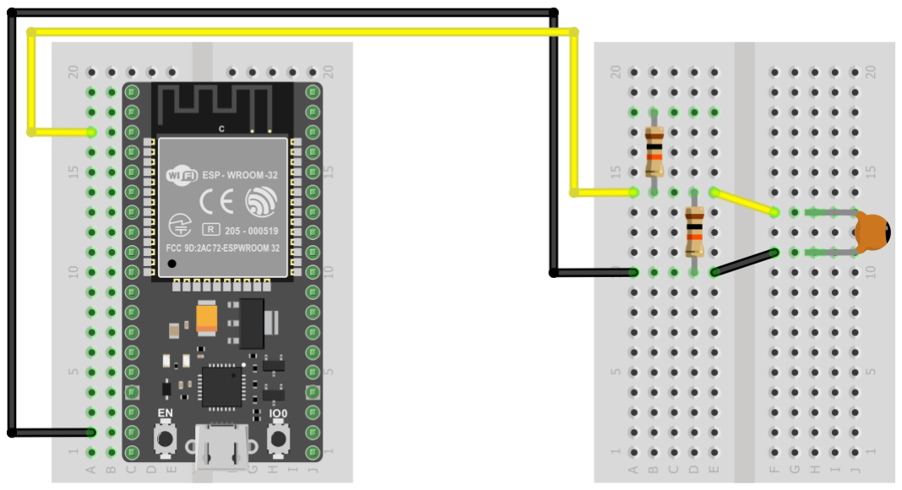
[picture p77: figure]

# The final step in the electronic assembly of this demonstrator is to connect the motor to the previous setup. One of its terminals should be connected to GND, and the other

terminal should be connected to the input of the voltage divider assembled earlier. The completed setup is presented below.


39

# Let's check that the setup of this Demonstrator works correctly by using the following code snippet, where we only read the output of the voltage divider connected to the ESP32. By rotating the motor's rotor, we will see how the measurement gives different

values through the Serial Monitor.

// Initialization block

void setup() {

// We initialize the Serial Monitor

Serial.begin(115200);

}

// Main loop of the code

void loop() {

// We take the measurement from the pin connected to the output of the voltage

//divider

int medicion = analogRead(39);

// We display the measurement on the Serial Monitor

Serial.println(medicion);

}

40

# 1. 3. 2. Mechanical Assembly

# The components of this demonstrator are as follows:

Elemento | Cantidad | Descripción | Imagen
Base | 1 | It is the top section that secures the moving components, such as the blades and the motor shaft. It provides stability and allows the system to operate smoothly, facilitating the proper transfer of energy from the blades to the generator.
Drawer | 1 | It is the base that connects the different sections of the device, providing structural support and ensuring proper alignment between the motor, blades, and other essential components for its operation.
Motor socket | 1 | This component will support and stabilize the motor, whose shaft will be connected to the bearing disc. This design will allow the connection of output pins, which will emit signals indicating the presence of movement.
Big L blade | 6 | It is a fixed blade that does not move. It is designed to be part of the static structure of the demonstrator, contributing to the overall stability and balance of the system.

41
Small L blade | 6 | It is a fixed blade that does not move, smaller than the previous piece. It is designed to be part of the static structure of the demonstrator, contributing to the overall stability and balance of the system.
Square blade | 8 | It is one of the key moving blades that rotates when driven by the wind. Its square design efficiently captures the wind's kinetic energy and converts it into rotational movement.
Big disc | 2 | It is a key component that serves as a structural support for the moving blades. This disk is designed to rotate when the blades capture the wind, transferring the rotational movement to the system's central shaft.
Small disc | 3 | It is a static component that does not move. Its main function is to act as part of the device's structural support, helping to maintain the proper alignment and stability of the moving elements, such as the blades and large disks.
Bearing disc | 1 | It is a crucial component used to reduce friction between the system's moving parts. This disk acts as a rotational support, allowing components like the Large Disk and the blades to spin smoothly and efficiently around

42
| | the central shaft.
Top | 1 | It is a structural component placed at the top of the assembly, ensuring that all internal elements are protected and properly aligned.
Bearing | 1 | It is a mechanical component that allows rotating elements, such as the disks and blades, to move with minimal friction.
Wood joints | 3 | It is a structural component used to connect and secure the different wooden parts of the device.

# The following shows how the demonstrator assembly is carried out:

Note: It is necessary to insert the 10-tooth gear onto the DC motor shaft before starting the assembly of the demonstrator.

43

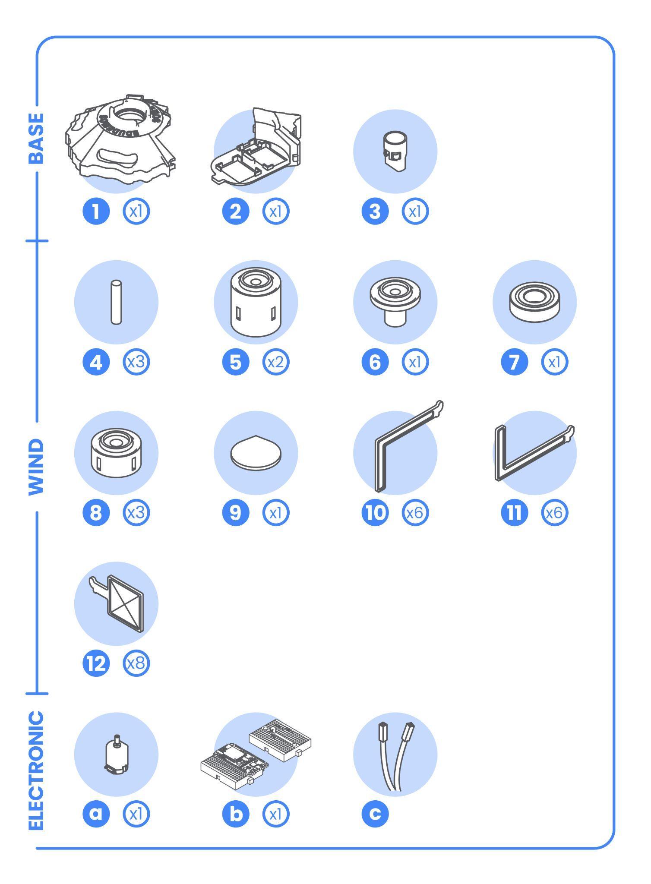
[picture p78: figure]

44

45


46

47


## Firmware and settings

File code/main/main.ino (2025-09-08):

/*
* This file is part of the EduDemoS 3x1 Demonstrator which is
* co-funded by the European Union.
* Copyright (C) 2025  Fundación Sergio Alonso
*
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
* You should have received a copy of the GNU General Public License
* along with this program.  If not, see <http://www.gnu.org/licenses/>.
*/

 
#include <WiFi.h>
#include <WiFiClient.h>
#include <HTTPClient.h>
#include <ArduinoJson.h>
#include "AdafruitIO_WiFi.h"
#include "DHT.h"
#include <ESP32Servo.h>
#include <ArduinoOTA.h>
#include "config.h"

// Pin definitions and constants
#define DHTPIN 32
#define DHTTYPE DHT11
#define ledPin1Cold 18
#define ledPin2Good 19
#define ledPin3Heat 21
#define ldrPin1 34
#define ldrPin2 35
#define servoPin 25
#define DcMotorPin 39
#define SolarPin 36
#define SENSOR_INTERVAL_5_MIN 300000
#define SENSOR_INTERVAL_10_SEC 10000
#define OFFSET 550
#define OFFSETLDR 300 //Difference between LDR1 and LDR2, (each case are different), look for yor personal value

WiFiServer telnetServer(23); 
WiFiClient telnetClient;

// Voltage divider resistances definitions
const float R1 = 1000.0; // 1kΩ resistor
const float R2 = 1000.0; // 1kΩ resistor

// Global variables
DHT dht(DHTPIN, DHTTYPE);
Servo myServo;

// Variables to store LDR sensor readings
int ldrValue1 = 0;
int ldrValue2 = 0;
int averageLdrValue = 0;

// Servo configuration variables
int servoPos = 100;  // Initial servo position in the middle (90 degrees)
int servoStep = 10;  // Servo movement increment/decrement
int tolerance = 150; // Tolerance to avoid small movements

AdafruitIO_WiFi io(AIO_USERNAME, AIO_KEY, WIFI_SSID, WIFI_PASS);
AdafruitIO_Feed *temperature = io.feed("temperature");
AdafruitIO_Feed *humidity = io.feed("humidity");
AdafruitIO_Feed *ldrFeed = io.feed("ldr");
AdafruitIO_Feed *ldr1Feed = io.feed("ldr1Feed");
AdafruitIO_Feed *ldr2Feed = io.feed("ldr2Feed");
AdafruitIO_Feed *microvoltsMotorDcFeed = io.feed("microvoltsMotorDc");
AdafruitIO_Feed *microvoltsSolarFeed = io.feed("microvoltsSolar");
AdafruitIO_Feed *ledHighFeed =  io.feed("ledHighFeed");
AdafruitIO_Feed *ledGoodFeed =  io.feed("ledGoodFeed");
AdafruitIO_Feed *ledColdFeed =  io.feed("ledColdFeed");
AdafruitIO_Feed *wifiFeed =  io.feed("wifiFeed");
float lastMicrovolts = 0;

void setup() {
  Serial.begin(115200); // Start serial communication at 115200 baud rate
  analogReadResolution(12); // ESP32 has a 12-bit ADC
  analogSetAttenuation(ADC_11db); // Set attenuation for higher sensitivity
  pinMode(4, INPUT);

  //setupWiFi(); // Setup WiFi connection
  //setupOTA(); // Setup OTA for remote updates
  setupDHT(); // Setup DHT sensor
  setupLEDsAndServo(); // Setup LED pins and servo

  // Create tasks
  xTaskCreatePinnedToCore(
    readSensorTask1,   // Task function
    "ReadSensorTask1", // Name of the task
    4096,             // Stack size
    NULL,              // Task input parameter
    1,                 // Priority of the task
    NULL,              // Task handle
    0                  // Core where the task should run
  );

  xTaskCreatePinnedToCore( 
    readSensorTask2,   // Task function
    "ReadSensorTask2", // Name of the task
    4096,             // Stack size
    NULL,              // Task input parameter
    1,                 // Priority of the task
    NULL,              // Task handle
    1                  // Core where the task should run
  );

  xTaskCreatePinnedToCore(
    readDcMotorVoltageTask,   // Task function
    "readDcMotorVoltageTask", // Name of the task
    4096,             // Stack size
    NULL,              // Task input parameter
    1,                 // Priority of the task
    NULL,              // Task handle
    1                  // Core where the task should run
  );

  xTaskCreatePinnedToCore(
    readSolarVoltageTask,   // Task function
    "readSolarVoltageTask", // Name of the task
    4096,             // Stack size
    NULL,              // Task input parameter
    1,                 // Priority of the task
    NULL,              // Task handle
    1                  // Core where the task should run
  );
}

void loop() {
  //handleOTA(); // Handle OTA updates
  //io.run(); // Maintain connection to Adafruit IO
}

void setupWiFi() {
  int retries = 0;
  const int maxRetries = 5;

  WiFi.begin(WIFI_SSID, WIFI_PASS);
  Serial.print("Connecting to WiFi");

  while (WiFi.status() != WL_CONNECTED && retries < maxRetries) {
    delay(1000);
    Serial.print(".");
    retries++;
  }

  if (WiFi.status() == WL_CONNECTED) {
    Serial.println("\nConnected to WiFi");
    // Send microvolts to Adafruit IO
    wifiFeed->save(WIFI_SSID);
  } else {
    Serial.println("\nWiFi connection failed. Restarting...");
    ESP.restart();
  }

  connectToAdafruitIO();
}

void connectToAdafruitIO() {
  Serial.print("Connecting to Adafruit IO");
  io.connect();

  int retries = 0;
  const int maxRetries = 5;

  while (io.status() < AIO_CONNECTED && retries < maxRetries) {
    Serial.print(".");
    delay(500);
    retries++;
  }

  if (io.status() < AIO_CONNECTED) {
    Serial.println("\nFailed to connect to Adafruit IO. Restarting...");
    ESP.restart();
  }

  Serial.println("\nConnected to Adafruit IO");
}

void setupOTA() {
  // Start telnet server
  telnetServer.begin();
  telnetServer.setNoDelay(true);
  // Initialize ArduinoOTA for over-the-air updates
  ArduinoOTA.setHostname("ESP32-OTA");
  ArduinoOTA.setPassword("admin"); // Uncomment to set a password for OTA updates
  // Define OTA event handlers
  ArduinoOTA.onStart([]() {
    String type;
    if (ArduinoOTA.getCommand() == U_FLASH) {
      type = "sketch";
    } else { // U_SPIFFS
      type = "filesystem";
    }
    Serial.println("Start updating " + type);
  });
  ArduinoOTA.onEnd([]() {
    Serial.println("\nOTA Update Finished");
  });
  ArduinoOTA.onProgress([](unsigned int progress, unsigned int total) {
    Serial.printf("Progress: %u%%\r", (progress / (total / 100)));
  });
  ArduinoOTA.onError([](ota_error_t error) {
    Serial.printf("Error[%u]: ", error);
    if (error == OTA_AUTH_ERROR) {
      Serial.println("Auth Failed");
    } else if (error == OTA_BEGIN_ERROR) {
      Serial.println("Begin Failed");
    } else if (error == OTA_CONNECT_ERROR) {
      Serial.println("Connect Failed");
    } else if (error == OTA_RECEIVE_ERROR) {
      Serial.println("Receive Failed");
    } else if (error == OTA_END_ERROR) {
      Serial.println("End Failed");
    }
  });
  ArduinoOTA.begin(); // Start the OTA service
  Serial.println("OTA Ready");
}
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

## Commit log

2025-07-11 Mirror original data from 28.05.2025
    [Aspa L grande_V3_x6.stp, Aspa L pequeña_V3_x6.stp, Aspa cuadrada_V4_x8.stp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]
2025-09-03 3x1 Assembly video
2025-09-03 Edudemos_Video printing 3x1

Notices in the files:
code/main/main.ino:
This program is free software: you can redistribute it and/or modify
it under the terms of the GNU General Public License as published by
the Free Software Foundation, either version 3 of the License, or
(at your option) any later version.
